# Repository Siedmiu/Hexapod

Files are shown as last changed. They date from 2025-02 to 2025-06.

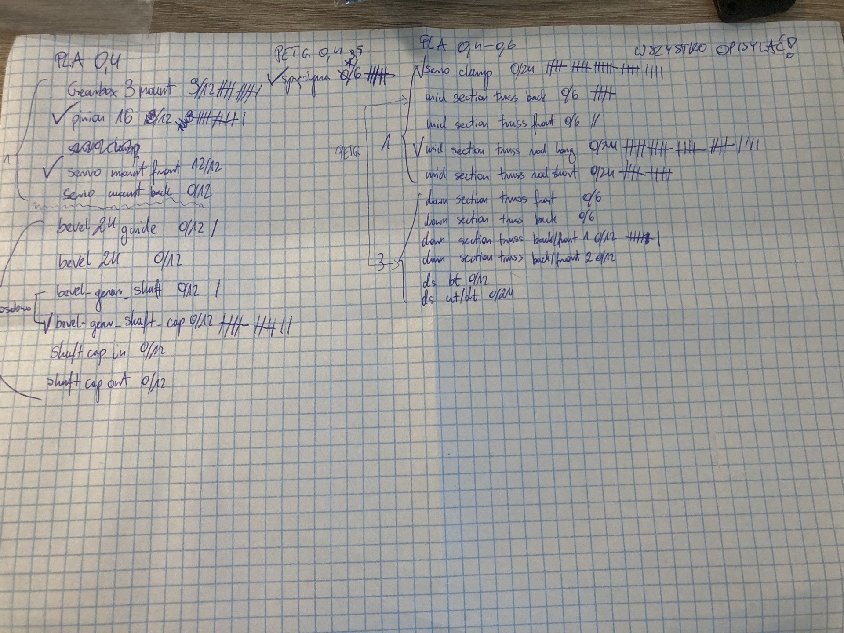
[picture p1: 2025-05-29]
hardware/3D models printing/DRUKOWANIE PROTO/printing progres/29.05.2025 _progress_note.jpg

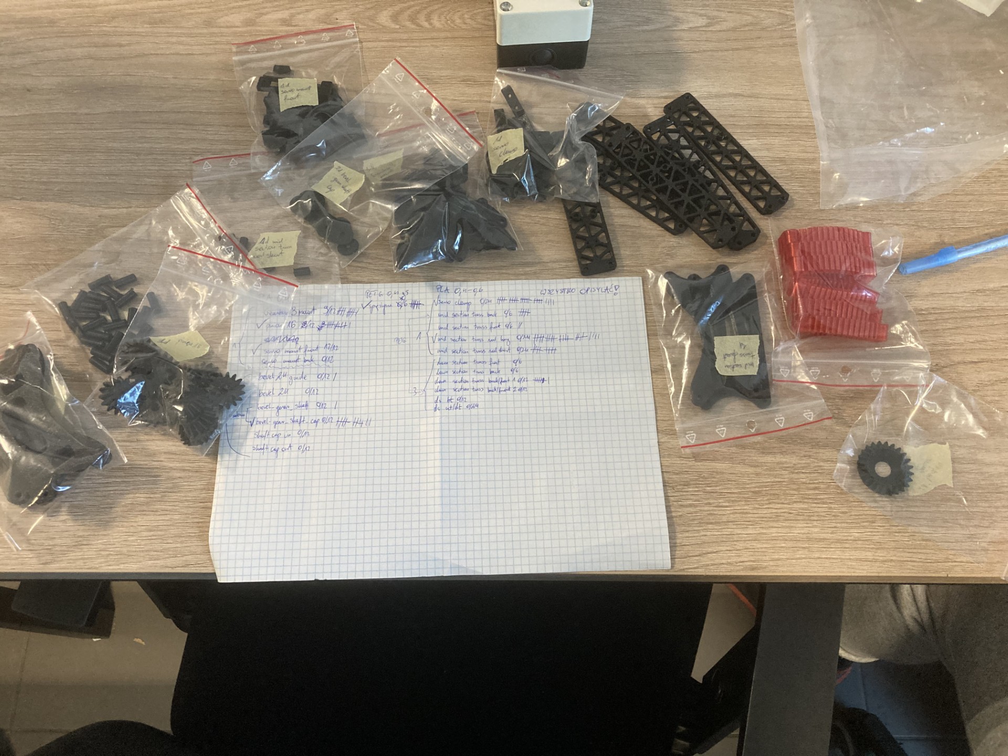
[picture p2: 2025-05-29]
hardware/3D models printing/DRUKOWANIE PROTO/printing progres/29.05.2025_printed_parts.jpg

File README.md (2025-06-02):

# Hexapod Robot Project

We are a group of students from Gdańsk University of Technology. Our goal is to create a 6 legged spider robot or a "Hexapod" in short.
Our current goals include the ability to **traverse difficult terrain**, **remote control** via an **android app**. Multiple walking algorithms are going to be implemented and tested.
Hexapod capabilities planned for the future include autonomous walking with the ability to follow objects and people using neural networks and computer vision algorithms.

Our simulation stack uses **ROS** and **Gazebo**, with **Python** for gait planning. The physical Hexapod is controlled by an **ESP32**, and all structural components are designed for **3D printing**.
For more information please visit our simulation repository: https://github.com/Siedmiu/Hexapod-Gazebo-Simulation

af067df6-a745-4674-9efd-3d1703f9f18c

## Milestone roadmap:

### Milestone I:
- [x] Complete Mechanical construction.
- [x] Preliminary simulation, ROS + Gazebo configured, single leg movement.

### Milestone II:
- [x] Production of parts and electronics procurement.
- [x] Hexapod assembly.
- [x] Simulating planned walking gaits.
- [x] Straight line walking tests.
- [x] ROS and manual remote control.

### Intermission -> New Design
- [x] New Hexapod Design.
- [x] Production of parts and electronics procurement.
- [x] Straight line walking simulation tests.
- [ ] Hexapod assembly.

### Milestone III:
- [ ] Full walk gait implementation.
- [ ] Tests and performance measurement.
- [ ] Finished project documentation.

Screenshots_2025-05-16-08-47-24

## Requirements:
Ubuntu 24.04 LTS, ROS Jazzy Jalisco, applicable Gazebo version

## Documentation and Setup:
Complete documentation, setup instructions, and Docker files will be available upon full release.

## Contributing:
This is a university-led project, and external contributions are not accepted until its conclusion.

## Related Repositories:
Android application repository: https://github.com/Siedmiu/Hexapod-Android-Application

Gazebo, Ros and simulation repository: https://github.com/Siedmiu/Hexapod-ROS2-System

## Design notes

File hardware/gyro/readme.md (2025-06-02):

These files contains code for acquiring and dealing with data provided by MPU-6050

gyro_write.ino is a script for Arduino to acquire data from gyroscope
Write.py is a script that writes the data to .csv file
traj.py calculates trajectory based of the data about angles and acceleration

============================================================================

_dmp files works as these above but are using DMP which provides better data

trajectory_integrated calculates trajectory using two data sets from IMU as now uses simple complementary filter

MPU-6050 datasheet: https://invensense.tdk.com/wp-content/uploads/2015/02/MPU-6000-Datasheet1.pdf

================19.04.2025==============
I am testing an alternative approach, and created new implementation.
The program runs through Matlab and directly connects to the esp, remember to define the COM port.

I want to use the onboard Digital Motion Processor (DMP) to get accurate orientation data while minimizing drift.

Data looks promising with minimal diviation and fast responses, but the acceleration scaling
needs to be fixed.

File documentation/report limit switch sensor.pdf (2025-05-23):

Autor: Mikołaj Goździelewski
Temat: Analiza możliwości implementacji krańcówki z elementem sprężystym w Gazebo

Celem jest zasymulowanie przełącznika krańcowego w środowisku Gazebo Harmonic, gdzie aktywacja krańcówki nie zachodzi bezpośrednio po dotknięciu ziemi, lecz po ugięciu elementu sprężystego. Oznacza to, że symulacja musi wykryć nie sam kontakt, lecz odpowiednio dużą siłę lub ugięcie wywołane naciskiem robota na podłoże.

## Potencjalne rozwiązania:

- model sprężyny + Contact Sensor
- Force-Torque Sensor

## Model sprężyny + Contact Sensor

Podejście polega na stworzeniu modelu sprężyny z wykorzystaniem „prismatic joint” i umieszczenie na jej końcu Contat Sensor. Pozwalałoby to na większy realizm symulacji oraz łatwą interpretację otrzymanych danych. Wadą rozwiązania jest duża złożoność modelu i możliwa niepotrzebna komplikacja symulacji. Rozwiązanie będzie bardzo wrażliwe na potencjalne rozbieżności modelu rzeczywistego i symulacyjnego jak i rozbieżności między fizyką w świecie realnym, a tą w programie.

## Force-Torque Sensor

Umieszczenie czujnika siły między dolną częścią nogi robota, a „podeszwą”, która w rzeczywistości nie istnieje. Rozwiązanie pozwala na dokładny pomiar siły i jest łatwe w integracji oraz nie wymaga dodatkowych skomplikowanych elementów jak działający model sprężyny. Wadą rozwiązania jest brak wizualizacji kontaktu, potencjalny problem z chwilową zmianą długości nogi oraz ręczne dobranie progu.

Wybrane rozwiązanie: Force-Torque Sensor
Uzasadnienie: Czujnik siły jest łatwiejszy w implementacji i mniej wrażliwy na potencjalne problemy z rozbieżnościami związanymi z fizyką w świecie rzeczywistym, a symulacji.

Wymagana konfiguracja:
Opcja 1 (inne dane z ROS dla programu z symulacji i robota):
- zdefiniowanie czujników siły w modelu dla każdej nogi
- skonfigurowanie mostu między Gazebo i ROS

- dodanie do kodu w python subskrypcji ROS, pobieranie wartości i przeliczanie ich Opcja 2:
- zdefiniowanie czujników siły w modelu dla każdej nogi
- napisanie własnego pluginu do Gazebo, który odczytywałby dane z API Gazebo i decydował czy jest siła wystarczająca do dotknięcia, a wtedy publikował wynik przez ROS

Plik XACRO:
Należy dodać wstawki <gazebo> w pliku, które będą wykorzystywane przez Gazebo podczas konwersji pliku URDF na SDF, wykorzystywany przez program.

Linki:
https://github.com/gazebosim/gz-sensors - repozytorium Gazebo o czujnikach, raczej nie przydatne
https://gazebosim.org/libs/sensors/ - strona Gazebo o czujnikach, pomocne jeśli nie wykorzystamy ROS do odczytów http://sdformat.org/spec?ver=1.12&elem=sensor#sensor_force_torque – strona SDF o czujnikach, przydatne do zmiany pliku XACRO https://gazebosim.org/api/sim/9/createsystemplugins.html - tutorial Gazebo o tworzeniu pluginów

Może przydatne linki do forów: https://robotics.stackexchange.com/questions/111546/need-for-gazebo-plugins-and-sdftutorial (https://robotics.stackexchange.com/questions/111546/need-for-gazebo-plugins-and-sdf-tutorial)
https://get-help.theconstruct.ai/t/documentation-for-gazebo-plugins/32571

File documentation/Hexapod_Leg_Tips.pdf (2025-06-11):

## High Friction Leg Tip Design for Walking Hexapod Robot: Design Process and Performance Evaluation

Grzegorz Lange

June 11, 2025

Abstract

This document presents the design process and performance evaluation of leg tip attachments for a walking hexapod robot. The primary objective was to address traction issues encountered on smooth and slippery surfaces through the development and testing of various rubber tip designs. Five different tip geometries were designed, manufactured, and tested: spherical base, flat base spherical, lattice spherical, flat with flower petals, and a hybrid design combining petals and lattice structures. Testing revealed that material selection is as critical as geometric design, leading to the development of silicone-based tips with TPU cores for optimal performance across various terrains.

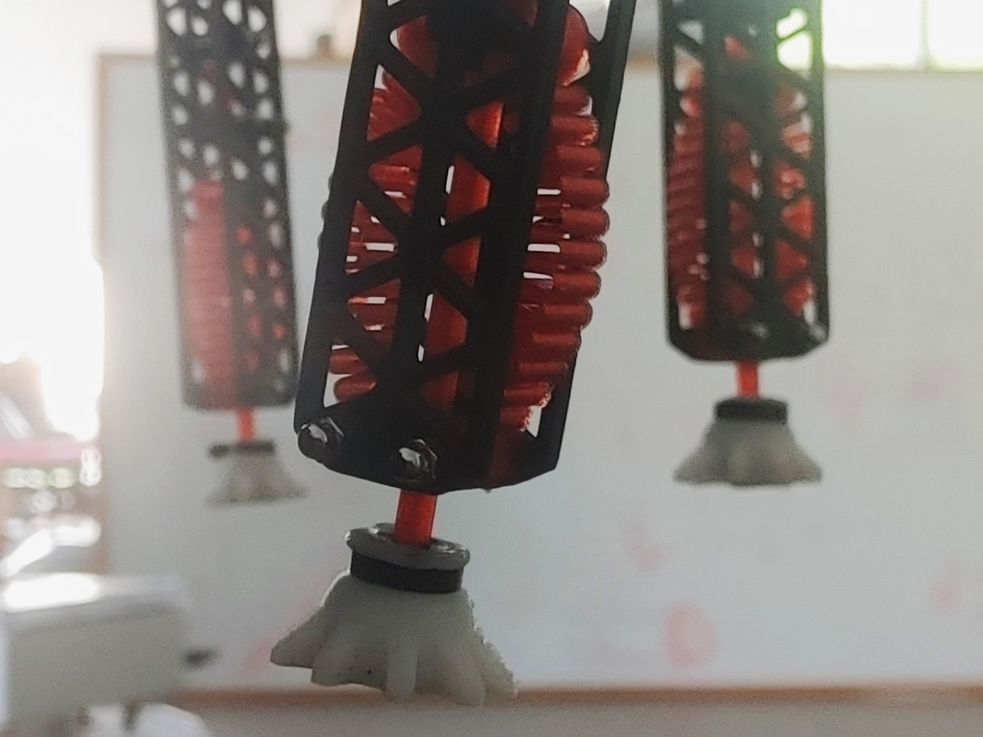
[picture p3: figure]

## 1 Introduction

Walking robots operating in diverse environments face significant challenges when encountering surfaces with varying friction characteristics. Hexapod robots, in particular, rely heavily on effective ground contact through their six legs to maintain stability and locomotion. This research addresses the critical issue of traction loss on smooth and slippery surfaces through systematic design and evaluation of specialized leg tip attachments.

### 1.1 Problem Statement

The hexapod robot experiences significant traction difficulties when operating on smooth surfaces such as polished floors, laminated surfaces, and other low-friction materials. These problems are amplified when dealing with small servomotors which are unable to maintain target position under heavy load. These conditions can lead to the following:

- Loss of locomotion control
- Reduced walking stability
- Inability to navigate certain terrains effectively
- Compromised performance of contact detection systems

### 1.2 Objectives

The primary objectives of this research are:

1. Design multiple leg tip geometries to improve surface traction
2. Evaluate performance across different surface types and conditions
3. Develop an optimal solution for indoor and outdoor applications

## 2 Design Methodology

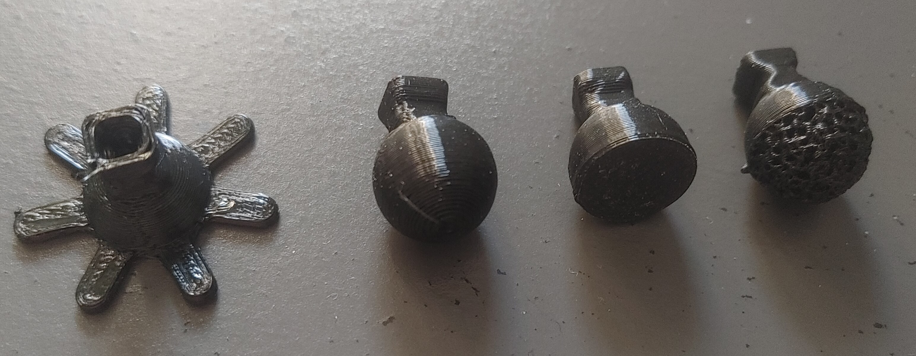
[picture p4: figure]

### 2.1 Design Concepts

Five distinct leg tip designs were developed and evaluated:

1. Spherical Base: Traditional rounded tip design serving as baseline
2. Flat Base Spherical: Flattened contact surface with spherical edges
3. Lattice Spherical: Spherical design with external lattice structure for deformation
4. Flat Flower Petals: Flat base with petal-like protrusions for increased contact area and adapt to angular changes
5. Hybrid (Petals + Lattice): Combined design incorporating both petal and lattice features

### 2.2 Material Selection

Two primary materials were investigated:

- TPU (Thermoplastic Polyurethane): Initial material choice for 3D printing capability. It is a soft material with great elastic deformation and a high coefficient of friction (COF).
- Silicone: Alternative material offering superior grip characteristics and high tackiness as a result of its high surface energy.

### 2.3 Manufacturing Process

### 2.3.1 TPU Components

TPU tips were manufactured using 3D printing technology, allowing complex internal geometries such as lattice structures and cavities. Custom Gcode approaches and advanced slicer features allowed for manufacturing exposed/external lattice structures creating textured surface for improved grip.

### 2.3.2 Silicone Components

Silicone tips were produced using custom molds for the external silicone lining combined with TPU cores for structural integrity. The manufacturing process involved

1. Mold design and fabrication
2. TPU core insertion for attachment interface
3. Silicone casting and curing

## 3 Testing and Evaluation

### 3.1 Testing Methodology

Performance evaluation was performed through single-leg testing on multiple types of surface. Each design was assessed using the following criteria:

- Deformation: Ability to conform to surface irregularities
- Contact Area: Maintenance of contact area under angular displacement
- Vertical Contact Area: Surface area in direct vertical contact
- Obstacle Hooking: Risks of engaging with surface features
- Terrain Penetration: Capability to penetrate soft surfaces and potential risks of jamming the legs into the ground.
- Shock Absorption: Energy dissipation during impact
- Dust/Sand Trap: Tendency to accumulate debris

### 3.2 Surface Types

Testing was carried out on the following surfaces:

- Smooth laminate
- Paper
- Hard foam
- Porous laminate

Due to the lack of professional testing equipment, friction performance was rated on a scale: low < medium < decent < good < excellent.

### 3.3 Shape Testing Results

Table 1: Design Characteristics and Mechanical Properties

Design | DeformationContact
Area/Angle

Vertical
Contact
Area

Obstacle
Hooking

Terrain Penetration

Shock Absorption

Dust/Sand
Trap
Spherical Base | Decent | Maintains same | Small | Low | Medium | Medium | No
Flat Base Spherical | Low | Low past certain an- gle | Large | Low | Low | Low | No
Lattice Spherical | Big | Maintains similar | Medium | Low | Medium | High | Yes
Flat + Flower Petals | Medium | Slightly decrease | Large | Medium/Low Low | Low | No
Hybrid | Big | Excellent | (remains
| | flat when tilted)
Large | Low | Low | Medium/Low Yes

Table 2: Surface Performance Comparison Across Different Materials

Design | Laminate Smooth | Paper | Hard Foam | Laminate Porous
Spherical Base | Low | Medium | Medium | Decent
Flat Base Spherical | Decent | Decent | Medium | Decent
Lattice Spherical | Low/Medium | Medium | Decent | Decent
Flat + Flower Petals | Decent | Decent | Medium | Decent
Hybrid | Decent | Decent | Medium | Medium

### 3.4 Shape Testing Key Findings

### 3.4.1 Flat Base

Flat base approach greatly increases the contact surface area, however it struggles with maintaining it even at shallow angles.

### 3.4.2 Flat Base with Flower Petals

Flower petals were added to directly address the issue with maintaining the contact surface area. The idea behind the flower petals is that, once the angle increases the flower petal will drag and deform the main tip surface.

### 3.4.3 Lattice structures

Incorporating the external lattice structure resulted in improvements in both traction and deformation. The open latices however have a tendency to accumulate sand and derbies, which results in sharp decline in performance. This approach is only suitable for clean environments and possible only using 3D printing technology.

### 3.4.4 Hybrid Design

The hybrid design combining petals and lattice structure demonstrated superior performance in maintaining contact area under angular displacement while providing adequate deformation characteristics.

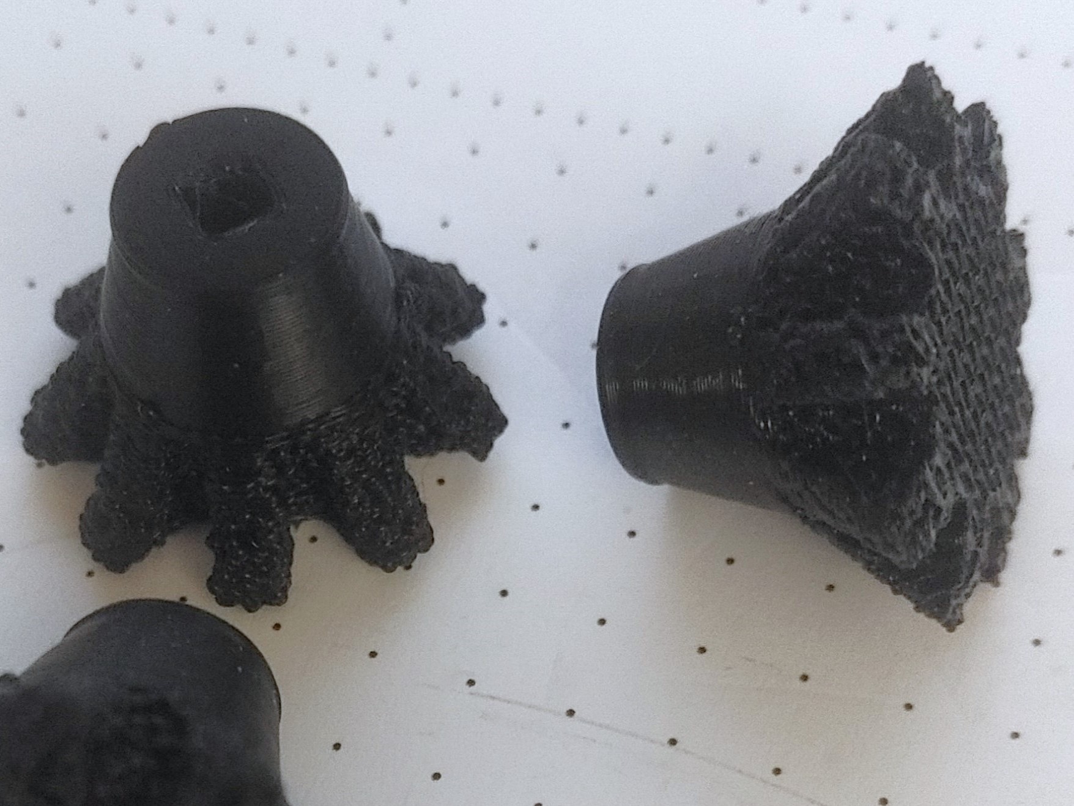
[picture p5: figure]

### 3.4.5 TPU Material Limitations

Despite geometric optimizations, TPU material exhibited insufficient grip on smooth surfaces, particularly on laminated floors where the robot continued to experience significant slipping.

### 3.4.6 Vertical Shock Absorption

The tip designs were engineered to exhibit poor vertical shock absorption performance. This approach was chosen to ensure predictability, since our Hexapod relies on shock absorbing springs coupled with contact detection switches. Allowing to much vertical compression of the tip could result in it getting twisted or sprained and loosing balance.

## 4 Material Transition and Optimization

### 4.1 Silicone Implementation

Based on testing results indicating material limitations, the design process transitioned to silicone-based tips. Key advantages of silicone include:

- Superior surface grip compared to TPU
- Enhanced deformation characteristics
- Better conformability to surface irregularities
- Reduced slipping on smooth surfaces

### 4.2 Hybrid Material Approach

The final design incorporates a hybrid material strategy:

- Silicone exterior: Provides optimal grip and deformation
- TPU core: Ensures structural stability and provides reliable attachment interface
- Elimination of vertical compression: TPU core prevents excessive deformation under load

### 4.3 Design Evolution

The silicone implementation underwent iterative improvement:

1. Initial silicone molding based on hybrid TPU design
2. Volume optimization: Second generation increased to 215% of original volume, for reliability the contact area should be as big as possible
3. Edge rounding to prevent stress concentration and cracking of the cast
4. Improved mold design for consistent manufacturing

### 4.4 Final Design

The final design consists of flat bottom surface with radially distributed petals structures that are connected via solid lofts to the main shaft. The tip has internal TPU core that extends up to 80 percent of the body. The design maximizes the contact area and conforms to the surface.

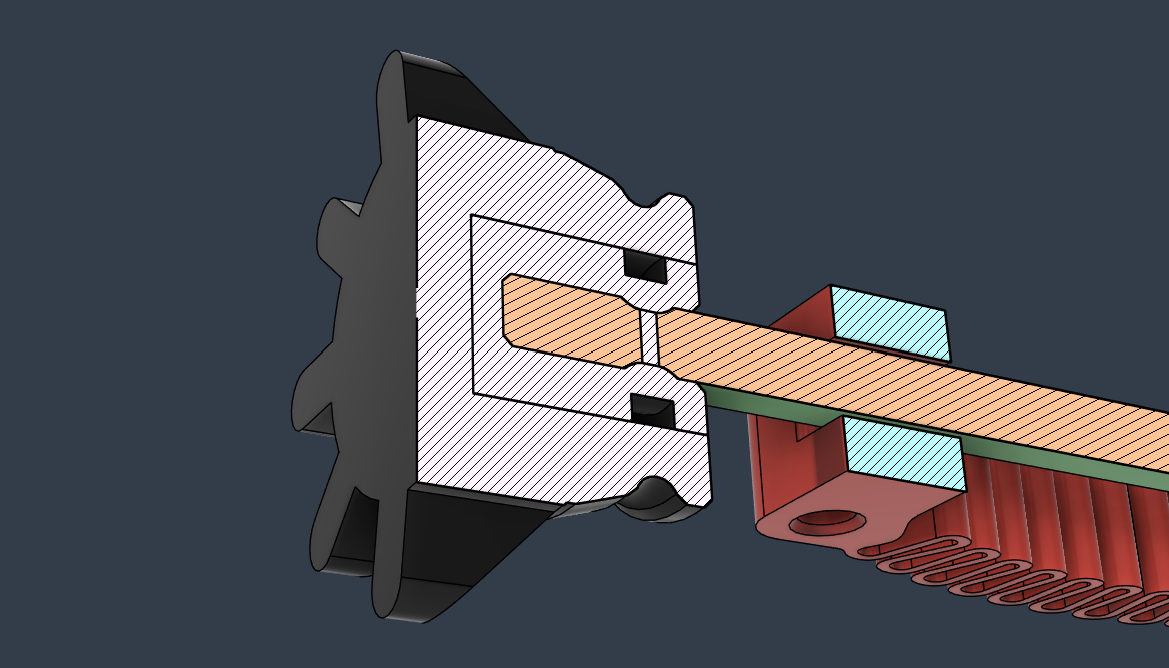
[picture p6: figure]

### 4.5 Final Design Tests

The design showed excellent friction performance on all of the tested surfaces. The TPU core decreased the vertical deformation, and it was rated as ”Medium” compared to other designs. The contact area was large and the main body of the tip is capable of maintaining its vertical position with relation to the ground for shallow angles. For larger angles the contact area decreases only slightly. The risks of terrain penetration and obstacle hooking are minimal, Dust and sand might stick to the surface, but is easy to clean.

## 5 Results and Discussion

### 5.1 Performance Validation

Testing confirmed the theoretical predictions regarding material performance:

- TPU designs, despite geometric optimization, remained insufficient for smooth surface traction
- Silicone implementation dramatically improved grip performance
- Hybrid material approach successfully balanced grip and structural integrity

### 5.2 Design Trade-offs

The evaluation revealed several important trade-offs:

- Deformation vs. Stability: Higher deformation improves surface conformity but may compromise structural stability
- Contact Area vs. Angular Performance: Larger flat surfaces provide better vertical contact but may lose effectiveness at angles
- Grip vs. Debris Accumulation: Designs with textures provide better grip characteristics but tend to trap more dust and sand

## 6 Conclusions and Possible Improvements

### 6.1 Conclusions

1. The hybrid design combining petals and lattice structure provides optimal geometric characteristics for indoor applications
2. Material selection is equally critical as geometric design for overall performance
3. Silicone material significantly outperforms TPU in terms of surface grip
4. Hybrid material approach (silicone exterior with TPU core) offers the best balance of performance characteristics
5. Develop surface-specific tip variants for specialized applications

### 6.2 Future Work

Future research directions include:

- Designs with surface dimples and or protrusions
- Designs with variable suction cups
- Investigation of smart materials for adaptive grip characteristics
- Integration of sensory capabilities within tip structures
- Long-term durability testing under operational conditions

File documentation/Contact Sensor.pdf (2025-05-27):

## Contact Sensor w Gazebo

Wstęp:
Celem zadania jest dodanie do symulacji czujników stykowych na nogach robota, które będą publikowały na wybranych topicach Gazebo informacje o kolizji. Doszło do niewielkiej zmiany planów względem raportu na temat researchu jak zrealizować w symulacji czujniki krańcowe ze sprężynkami. W tamtym tekście zdecydowałem o wykorzystaniu czujników siły, ale po naradzie z członkami grupy doszliśmy do wniosku, że uproszczenie zadania do czujniku stykowego nie powinno stanowić większego problemu. Na starcie muszę zaznaczyć, że zadanie nie zostało jeszcze wykonane. Do dokładniejszego zrozumienia tematu na szybko opiszę rzeczy, które uznałem za istotne do zrozumienia dalszego tekstu. Symulacja Gazebo składa się z plików Xacro, które opisują robota, pliku SDF, który opisuje świat oraz plików pythonowych, które pozwalają na uruchomienie symulacji. Pliki Xacro mają na celu usprawnienie pisania opisów robotów, dzięki zastosowaniu tagów MACRO, które są swego rodzaju funkcjami, które można wywołać przesyłając swoje parametry. Jedynym systemem plików obsługiwanym przez Gazebo jest SDF, co prowadzi do dużego problemu i konieczności translacji pliku Xacro na SDF, co niestety nie jest możliwe, gdyż Xacro opisuje nie plik SDF, a URDF, wymagany do innych programów. Translacja odbywa się przez najpierw zamianę Xacro na URDF, a następnie URDF na SDF. Translacje te można wykonać również komendami:

Translacja Xacro na URDF:
ros2 run xacro xacro nazwa_pliku.xacro > nazwa_pliku.urdf
Translacja URDF na SDF:
gz sdf -p nazwa_pliku.urdf > nazwa_pliku.sdf

Problemy (informacje zawarte w tym segmencie niekoniecznie są poprawne, są one tylko i wyłącznie moimi przemyśleniami, zdobytymi na bazie kilku godzin prób dodania czujników, szukania informacji na ich temat w internecie oraz konsultacji z ChatemGPT):

- Pluginy – do poprawnego korzystania z czujników styku potrzebne są odpowiednie pluginy, które należy dodać do pliku SDF, który opisuje świat, plugin czujnika styku to:
<plugin
filename="gz-sim-contact-system"
name="gz::sim::systems::Contact">
</plugin>
Niestety dodanie tego pluginu prawdopodobnie spowoduje błędy, skutkujące niepoprawnym uruchamianiem symulacji, jest to spowodowane tym, że domyślnie Gazebo korzysta z różnych pluginów, ale dodając własny domyślne nie są już wczytywane i należy dodać je własnoręcznie są to pluginy:
<plugin
filename="gz-sim-physics-system"
name="gz::sim::systems::Physics"> </plugin>
<plugin
filename="gz-sim-scene-broadcaster-system" name="gz::sim::systems::SceneBroadcaster"> </plugin>
<plugin
filename="gz-sim-user-commands-system" name="gz::sim::systems::UserCommands"> </plugin>

- Plik opisujący świat – możliwym problemem może również być brak lub niepoprawne zdefiniowanie pola kolizyjnego podłogi, powód zostanie dokładniej opisany w podpunkcie „Topic czujnika”
- Znacznik Gazebo – przez pisanie opisu robota w Xacro, a nie w SDF jest potrzeba korzystania ze znaczników <gazebo>, niestety tutaj pojawia się problem. Użycie znacznika <sensor> wewnątrz samego znacznika <gazebo> nie pozwoli na dodanie czujnika, podczas translacji z pliku URDF na SDF interpreter ignoruje wszystko czego nie rozumie, a nie rozumie znacznika <sensor>, więc ta sekcja zniknie w wynikowym pliku SDF, żeby tego uniknąć należy skorzystać ze znacznika <gazebo reference=”nazwa_linku”>. Taka składnia zmusza interpreter do umieszczenia zawartego segmentu wewnątrz linku, co spowoduje pojawienie się jego w drzewku opisującym model z GUI(interfejs graficzny) Gazebo.
Przykład składni:
<gazebo reference="nazwa_linku">
<sensor name='nazwa_sensoru' type='contact'> <contact>
<collision>nazwa_pola_kolizyjnego</collision> <topic>/nazwa_topic</topic>
</contact>
<always_on>1</always_on>
<update_rate>100</update_rate>
</sensor>
</gazebo>
- Problemy ze znacznikiem <collision> - do poprawnego działania czujnika styku, należy mu przypisać odpowiednie pole kolizyjne zawarte w znaczniku <collision>. W przypadku korzystania z plików Xacro oraz jointów typu „fixed”, podczas translacji dochodzi do zmian nazw pól kolizyjnych, co prowadzi do niepoprawnego określania pola przypisanego do czujnika. Nową nazwę pola kolizyjnego można sprawdzić w drzewku opisującym model w GUI Gazebo. Możliwy jest również problem z samą definicją pola kolizyjnego, gdyż na wszystkich znalezionych przeze mnie przykładach czujnik stosowany jest na prostych obiektach z prostymi polami kolizyjnymi złożonymi z pojedynczych znaczników <collision>, w naszym przypadku korzystamy z pola kolizyjnego składającego się z kilku znaczników <collision> co może być problemem.
- Topic czujnika – topic czujnika styku w Gazebo publikuje tylko w momencie wykrycia kolizji między przypisanym pole, kolizyjnym, a innym obiektem. Istnieje więc możliwość, że topic czujnika nie pojawia się z powodu złej definicji pola kolizyjnego lub braku odpowiedniej kolizji.
- Dokumentacja i przykłady – realizacji zadania nie ułatwia brak jakiejkolwiek sensownej dokumentacji lub przykładów. Gazebo Harmonic jest dość nowa, co powoduje problemy ze znalezieniem jakichkolwiek informacji o działaniu programu, a już szczególnie przykładów choć trochę zbliżonych skomplikowaniem do projektu „Hexapod”, powoduje to w dużej mierze działanie sposobem prób i błędów, poruszając się na oślep nie mając pojęcia, czy dana zmiana faktycznie przybliża do ukończenia zadania, czy może psuje kolejny element układanki.

Podsumowanie:
Nie udało mi się osiągnąć działającego czujnika styku w Gazebo i nie mam pojęcia gdzie może tkwić problem. Jest kilka potencjalnych miejsc, gdzie dochodzi do błędu, a są to:
- złe umieszczenie lub zdefiniowanie pluginu dla czujnika
- złe przypisanie pola kolizyjnego do czujnika
- źle zdefiniowanie pola kolizyjnego, niewystarczająca ilość danych dla Gazebo
- brak kolizji między polem kolizyjnym, a podłogą, co powoduje brak nadawania topicu czujnika
- brak lub zła definicja pola kolizyjnego podłogi w pliku opisującym świat.

A kto zrobi poprawnie działający Contact Sensor w Gazebo?
No WY
Pozdrawiam dr inż. Krzysztofa Nowickiego

Przydatne(lub nie) linki:
Działający Contact Sensor dla prostego modelu (plik SDF) https://github.com/gazebosim/gz-sim/blob/gz-sim8/examples/worlds/contact_sensor.sdf Dokumentacja Gazebo Harmonic na temat czujników: https://gazebosim.org/docs/harmonic/sensors/

Autor: Mikołaj Goździelewski

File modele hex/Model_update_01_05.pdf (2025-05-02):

Model update 01.05.2025

In order improve consistency, reduce reliance on precise tolerances, and reinforce the first joint, several changes have been made to the model.
The impact that those changes have on the simulation is negligible.

Joint 0 changes:

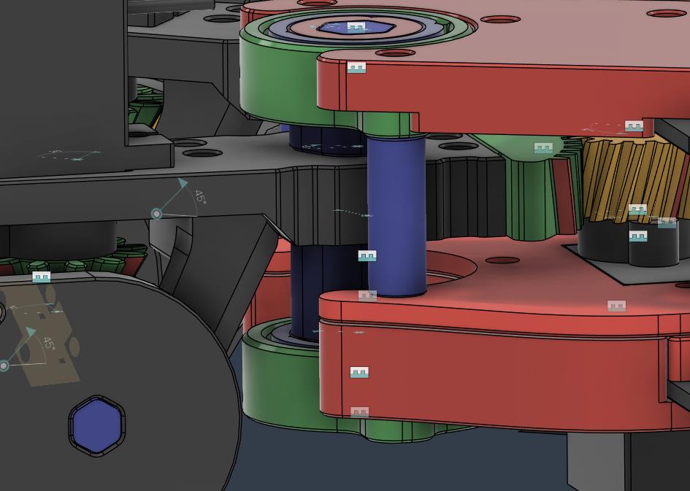
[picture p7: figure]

The mounting bolt hole on the “up section/leg attachment/servo holder” has been relocated to ensure space for a new set of reinforcement roods. The rods prevent tension build-up from the torque (Y CCW for left legs of the hexapod) when the legs are lifted off the ground.
Together with slots on the servo holder, the rods limit the motion preventing de-meshing of the gears.

Joint 3 changes:

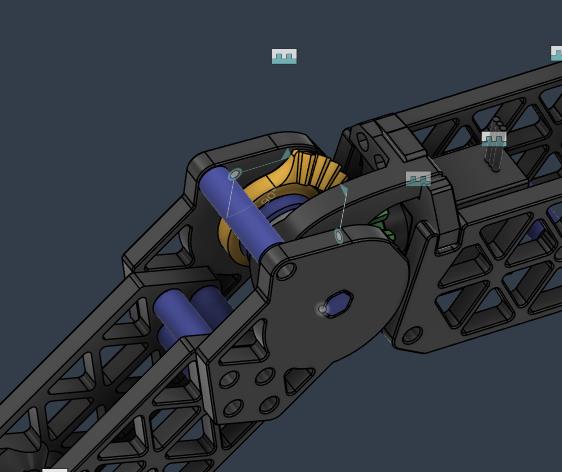
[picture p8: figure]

New reinforcement rod has been added to ensure that the material won’t bend outwards and skip a step on the gear assembly. This rod also prevents de-meshing of the gear assembly when a CCW rotation is applied past the range of motion.

Bug fixes:
Fixed missing holes on the platform mounting clips and bearing center hexagonal holes that were created due to an incorrect way that the Fusion handles downstream changes.

Misc:
Reduced the radius of the ball bearings mounting parts.
Changed how rods tolerance is calculated.
Numerous small changes with no downstream effect.

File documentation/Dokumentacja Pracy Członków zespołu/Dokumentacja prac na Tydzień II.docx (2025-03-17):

# Dokumentacja prac na Tydzień II

Skrócony spis prac wykonanych przez członków zespołu:

- Mariia Krykun: prace nad symulacją w ROS2; Komunikacja ROS2 z ESP32, przesyłanie obliczeń
- Bartłomiej Bąk: Symulacja python ruchu i kolizji
- Bartosz Babiński: Nauka i prace nad symulacją w Gazebo; Integracja modelu w Gazebo
- Grzegorz Lange: Poprawki mechaniczne; Projekt łożysk
- Julia Hrycyna: Symulacja Python ruchu w 2D i 3D
- Mateusz Boniecki: Nauka Kotlin + prace nad aplikacją
- Mikołaj Goździelewski: Integracja modelu w Gazebo; Nauka i research Gazebo
- Natan Tułodziecki: Kurs Android Studio; wybór MK
- Miłosz Kaszubowski: Wyliczenia prądowe; Wybór dostawców elementów
- Paulina Lokś: Kurs Android Studio

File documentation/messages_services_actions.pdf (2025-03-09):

Communication in ROS

Effective communication between different modules is crucial in a robotic system, enabling seamless data exchange and coordination. In ROS (Robot Operating System), three primary communication methods facilitate interactions between different components: messages, services, and actions. Each method serves a unique purpose, depending on whether the communication needs to be continuous, request-based, or interactive with feedback.

Example of a Trash-Picking Robot

To understand how these communication methods work, consider a trash-picking robot. This robot continuously detects trash, moves toward it, picks it up, and deposits it into a bin. Its software consists of three key modules:

1. Perception – Detects and identifies
trash.
2. Brain – Processes the perception data and decides on actions.
3. Actuation – Controls the robot’s
movement and physical interactions.

For the robot to function correctly, these

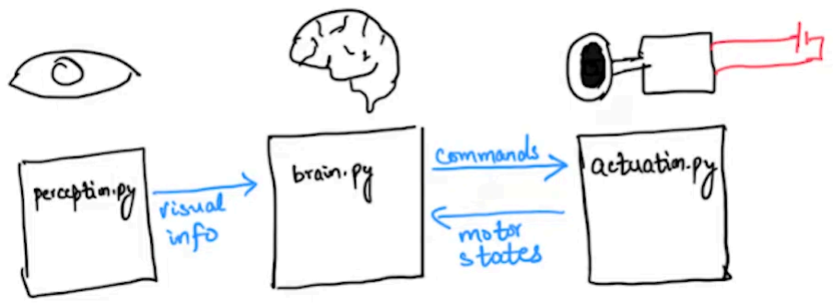
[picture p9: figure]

modules must exchange data efficiently. The perception module must communicate visual information to the brain, the brain must send movement commands to the actuation module, and the actuation module must report motor states, such as battery levels, back to the brain.

Communication Method 1: Messages (Topics)

One of the fundamental communication methods in ROS is message passing via topics. A topic acts as a channel where one module publishes data, and other modules subscribe to receive updates. This model is useful for continuous, asynchronous data exchange.

- In the trash-picking robot, the perception module publishes trash detection data on a specific topic.
- The brain subscribes to this topic, staying updated on detected trash.
- This setup ensures that whenever the perception module identifies trash, the brain module immediately receives the information.

The key characteristic of topic-based messaging is asynchronous communication—the publisher can send updates at any time, and subscribers receive them as they occur without needing to request data explicitly.

Communication Method 2: Services

Unlike topics, services allow a module to request specific information or trigger an action from another module in a client-server model. This method is useful for request-response interactions rather than continuous data flow.

- In the trash-picking robot, the brain may need to check the battery status before executing a movement command.
- The brain sends a request to the actuation module (server) to retrieve battery information.
- The actuation module responds with the requested battery level.

This approach ensures that the brain only retrieves the data when necessary, reducing unnecessary data transmission. Services also support requests with parameters, allowing for specific queries (e.g., checking the battery level of a particular motor).

Communication Method 3: Actions

Actions are a more advanced communication method used for tasks that require feedback and the ability to cancel execution. Unlike services, which are single request-response interactions, actions provide ongoing status updates during task execution.

- Suppose the brain instructs the actuation module to move the robot to a specific position.
- The actuation module continuously sends feedback about the robot’s current location.
- If needed, the brain can cancel the movement command mid-execution—a feature not available with services.

Actions are particularly useful for long-running operations where real-time monitoring is necessary, such as motion control, navigation, and robotic arm manipulation.

Differences in ROS Versions

One notable difference between ROS 1 and ROS 2 is how they handle service calls. In ROS 1, service calls are blocking, meaning the system must wait for a response before proceeding. In ROS 2, non-blocking calls allow the program to continue execution while waiting for a response, improving efficiency in distributed systems.

Conclusion

ROS provides three primary communication methods to handle different types of interactions in a robotic system:

1. Messages (Topics) – Used for continuous, asynchronous data sharing.
2. Services – Best suited for request-response interactions.
3. Actions – Ideal for tasks requiring feedback and the ability to cancel execution.

Choosing the appropriate method depends on the specific needs of the system. Understanding these communication mechanisms is essential for designing efficient, scalable robotic applications.

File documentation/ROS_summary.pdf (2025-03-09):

Understanding ROS: The Robot Operating System

What is ROS?

ROS (Robot Operating System) is a widely used middleware designed to simplify the development of robotic systems. While it is not a traditional operating system, it provides essential tools and services that help manage communication between different components in a robotic system. ROS facilitates message passing, package management, and hardware abstraction, making it easier for developers to build complex robotic applications.

The Need for ROS

Robotic systems often consist of multiple independent modules that must work together efficiently. Without a structured framework, managing communication and coordination between these components can be challenging. ROS was created to address this issue by offering a standardized way to handle inter-process communication, ensuring seamless data exchange between various parts of a robot.

Example of a Robotic System

A useful way to understand ROS is by considering a humanoid trash-picking robot. This robot needs to perform tasks such as scanning the environment for trash, moving toward it, picking it up, and placing it in a bin. Its software stack can be divided into three key modules:

1. Perception – Detects and identifies trash in the environment.
2. Brain – Acts as the decision-making center, processing information from perception and determining the next action.
3. Actuation – Controls movement and executes the actions planned by the brain.

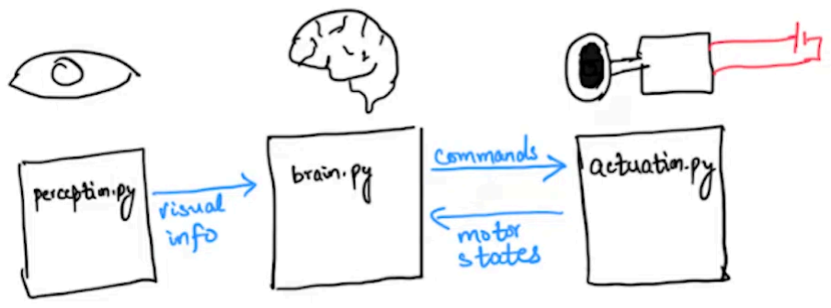
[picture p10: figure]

Efficient communication between these modules is critical for the robot to function correctly. The perception module informs the brain about detected trash, and the brain then instructs the actuation module to move accordingly.

Communication Methods in Robotic Systems

Two common methods are used to enable communication between different modules in a robotic system:

- Polling: The perception module continuously checks for trash and updates a shared memory location. The brain and actuation modules repeatedly check this memory to get updates. While functional, polling can be inefficient due to constant processing.
- Interrupts: A more efficient approach where modules only respond when an update occurs, reducing unnecessary processing and improving system responsiveness.

ROS helps manage these communication methods by providing a structured messaging system, ensuring efficient data exchange without requiring developers to handle low-level communication details manually.

ROS as Middleware

As middleware, ROS simplifies the process of integrating multiple components within a robotic system. It allows developers to focus on building individual modules without worrying about how they communicate. This abstraction is especially useful in distributed robotic systems, where different processes run independently but must share information in real time.

Package Management in ROS

ROS uses a package-based system to organize different functionalities into modular components. These packages contain specific functionalities such as motion control, sensor processing, or navigation.

- In ROS1, Catkin is the tool used for package management.
- In ROS2, Colcon is introduced, providing improved build efficiency and better dependency management.

This modular structure makes it easier for developers to maintain, reuse, and share components across different robotic projects.

Hardware Abstraction

ROS also provides a layer of hardware abstraction, allowing developers to integrate various hardware components without needing to understand their low-level details. Packages can be created to include drivers and embedded code for specific hardware, and these packages expose standardized ROS APIs. This makes it easier for other developers to use the hardware without directly interacting with its internal workings.

Open-Source Community and Reusable Packages

One of the biggest advantages of ROS is its large open-source community. Many pre-built ROS packages exist for common robotic functionalities, such as localization, mapping, and navigation. These packages can be used as plug-and-play modules, accelerating development and reducing the need to build everything from scratch. However, for specialized applications, custom ROS packages may still be necessary.

Conclusion

ROS plays a crucial role in modern robotics by providing a standardized framework for communication, package management, and hardware abstraction. It enables developers to build complex robotic systems more efficiently while benefiting from a vast open-source ecosystem. Understanding ROS is essential for anyone working with robotic applications, as it simplifies both software and hardware integration, making robotic development more accessible and scalable.

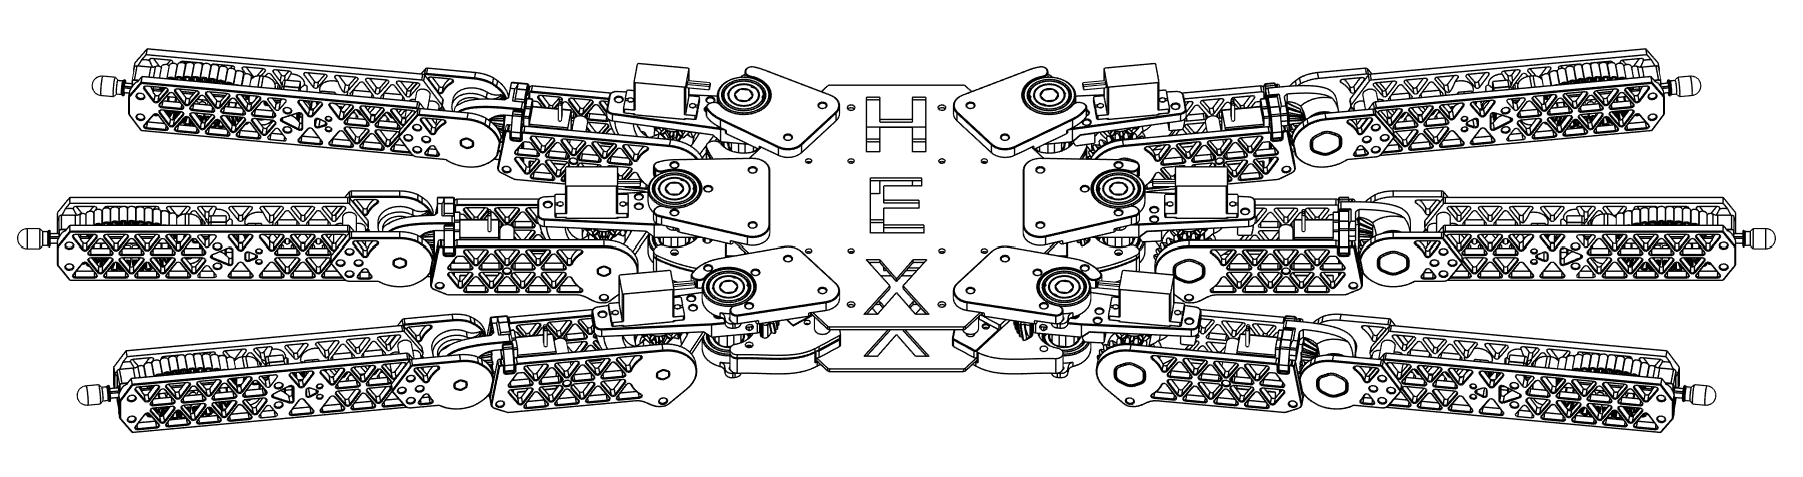
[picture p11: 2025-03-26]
images_new/straight.PNG

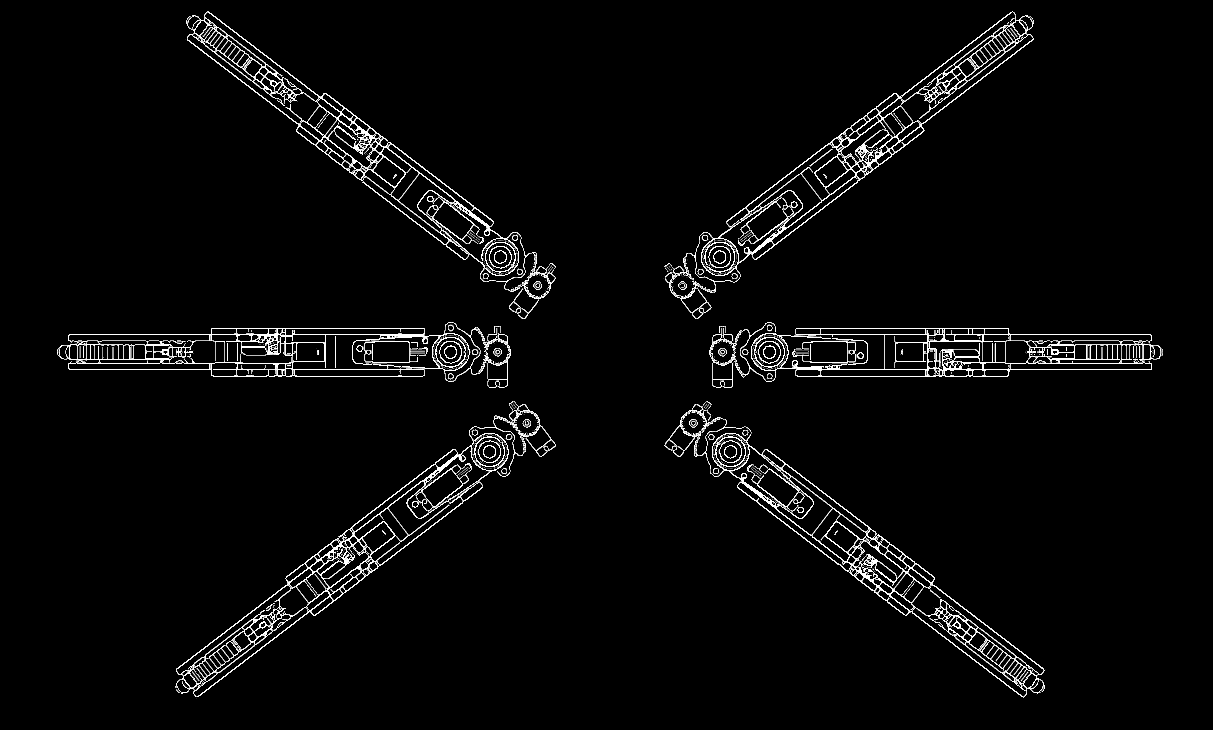
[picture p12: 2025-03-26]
images_new/top_legs_processed.png

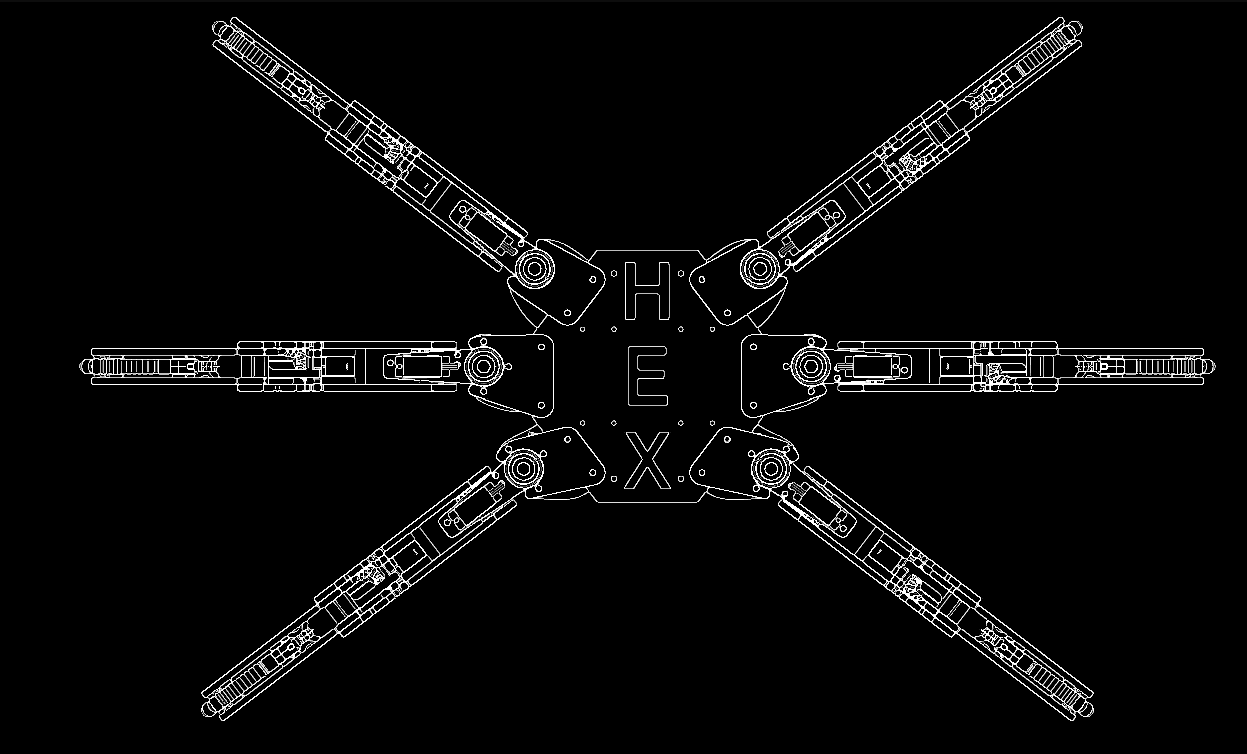
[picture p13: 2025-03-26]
images_new/full_top.PNG

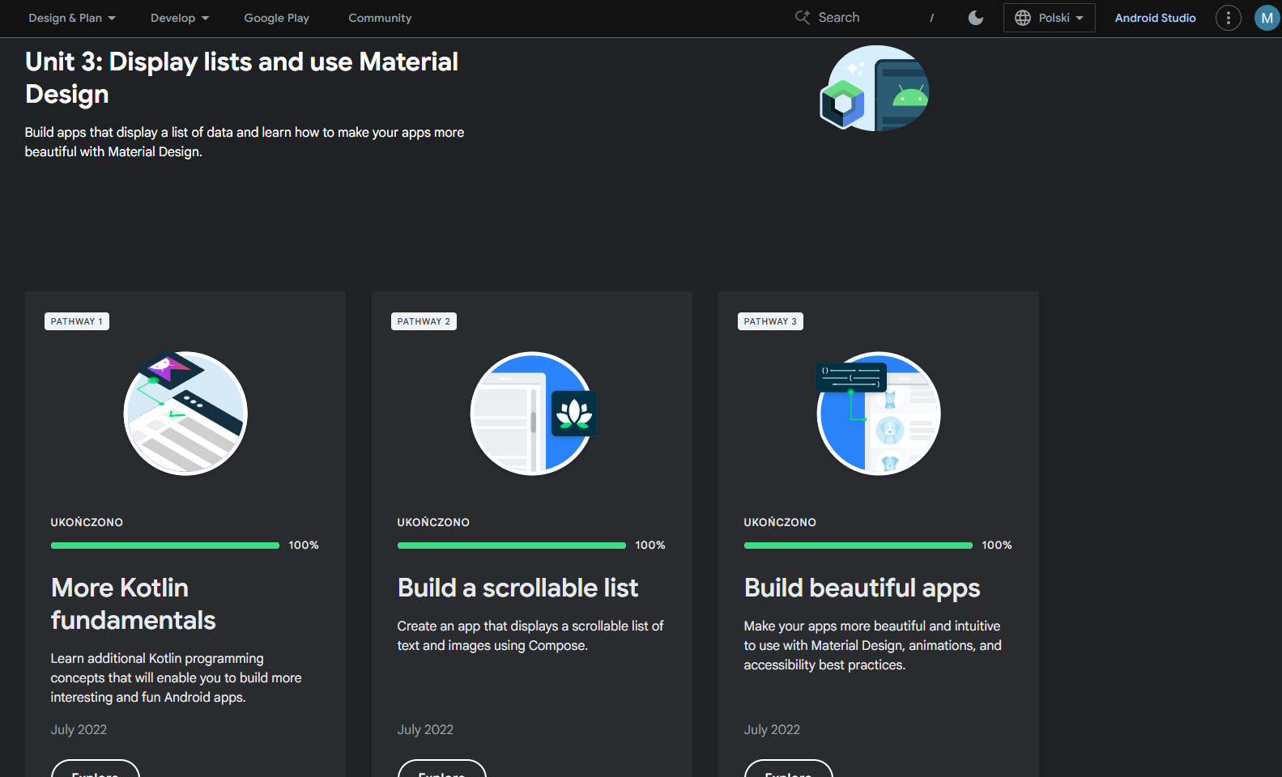
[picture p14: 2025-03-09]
documentation/Dokumentacja Pracy Członków zespołu/learning/Android Basics with Compose/Zrzut ekranu 2025-03-09 144319.png

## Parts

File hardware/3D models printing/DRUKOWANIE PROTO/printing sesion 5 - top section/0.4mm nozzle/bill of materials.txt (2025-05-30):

==========0.4==============
//bez kulek łożyskowych nie powinno być tarcia między elementami
// bearing outside(cage bottom(bearing inside))
bearing inside.stl		x12
bearing outside.stl		x12
cage bottom.stl			x12

Spur 16.stl			x6
Spur 32.stl			x6
Vertical Shaft.stl		x6

==========0.4 or 0.6========
Bearing Cap Up.stl		x6
Top Section Holder.stl		x6 //"kropelka" ustawiona ogonkiem do góry
Top Section Truss Back.stl	x6
Top Section Truss Front.stl	x6

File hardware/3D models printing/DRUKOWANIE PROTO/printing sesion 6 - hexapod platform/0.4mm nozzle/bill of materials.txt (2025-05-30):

==========0.4==============
support rod small.stl		x12
support rod.stl			x12
==========0.4 or 0.6========
Platform Top.stl		x1 (drukuje Miłosz)
Platform Down.stl		x1 (drukuje Miłosz)
bearing mount L0-5 down/top.stl x6 (każdy plik raz, drukuje Grzegorz)

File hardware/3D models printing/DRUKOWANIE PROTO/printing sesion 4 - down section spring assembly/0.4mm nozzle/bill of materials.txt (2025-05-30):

Części symeryczne oznaczone "/"

rod holder back/front.stl 	x12
Spring Rod.stl			x6
switch holder back/front.stl	x12
Spring				x6 already printed

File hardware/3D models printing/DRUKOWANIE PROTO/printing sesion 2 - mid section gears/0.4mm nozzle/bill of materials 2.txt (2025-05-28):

bevel 24 guide.stl 	x12
bevel 24.stl 		x12
Bevel_gear_shaft.stl 	x12
Bevel_gear_shaft_cap.stlx12
shaft cap in.stl 	x12
shaft cap out.stl 	x12

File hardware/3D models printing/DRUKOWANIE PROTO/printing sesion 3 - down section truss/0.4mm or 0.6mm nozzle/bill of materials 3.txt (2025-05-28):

Części symeryczne oznaczone "/"

Down Section Truss Front.stl 		x6
Down Section Truss Back.stl 		x6
Down Section Truss Back/Front 1.stl	x12
Down Section Truss Back/Front 2.stl	x12
ds bt.stl				x12
ds ut/dt.stl				x24

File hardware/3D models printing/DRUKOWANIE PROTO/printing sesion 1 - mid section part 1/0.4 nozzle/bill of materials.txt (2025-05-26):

KOPIA PLIKU DLA WYGODY

0.4 or 0.6 nozzle:
Mid Section Truss Back.stl x6
Mid Section Truss Front.stl x6
mid section truss rod long (identyczne modele) -> 24 sztuki
mid section truss rod short (identyczne modele) -> 24 sztuki
servo clamp.stl x24

0.4 nozzle:
servo mount back.stl x12
servo mount front.stl x12
pinion 16.stl x12
Gearbox 3 Mount.stl x12

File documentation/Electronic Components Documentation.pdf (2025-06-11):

# Electronic Components Documentation

### Project: [Your Project Name]

### June 11, 2025

## Contents

1 Overview | 2
2 Components | 2
3 Electrical Wiring Diagram | 3

## 1 Overview

This document describes the electronic components used in our project, along with their specifications and roles. The system is based on an ESP32 controller and includes servos, PWM drivers, sensors, and switches.

## 2 Components

### 2.1 MG996R Servo Motors (x18)

- Type: Digital high torque servo
- Operating Voltage: 4.8V–7.2V
- Stall Torque: Up to 11 kg.cm @ 6V
- Control Signal: PWM (Pulse Width Modulation)
- Application: Movement control (e.g., limbs, joints)

### 2.2 PCA9685 PWM Controller (x2)

- Channels: 16-channel 12-bit PWM
- Communication: I²C interface
- Power Supply: 5V logic level
- Used for controlling up to 32 servos with only two I²C addresses

### 2.3 POS-150-5-C Power Supply

- Output Voltage: 5V
- Output Current: Up to 30A (150W total)
- Usage: Powers servos and PCA9685 boards

### 2.4 Micro Endstop Switches (x6)

- Type: Momentary mechanical switches
- Usage: Limit/end position detection
- Triggered when component reaches physical boundary

### 2.5 ESP32-WROVER-DEV

- Microcontroller with Wi-Fi and Bluetooth
- Extra RAM (4MB PSRAM)
- GPIO, I²C, SPI support
- Central controller for the system

### 2.6 MPU6050 Accelerometers (x2)

- 3-axis gyroscope and 3-axis accelerometer
- Communication: I²C
- Used for motion sensing and orientation

## 3 Electrical Wiring Diagram

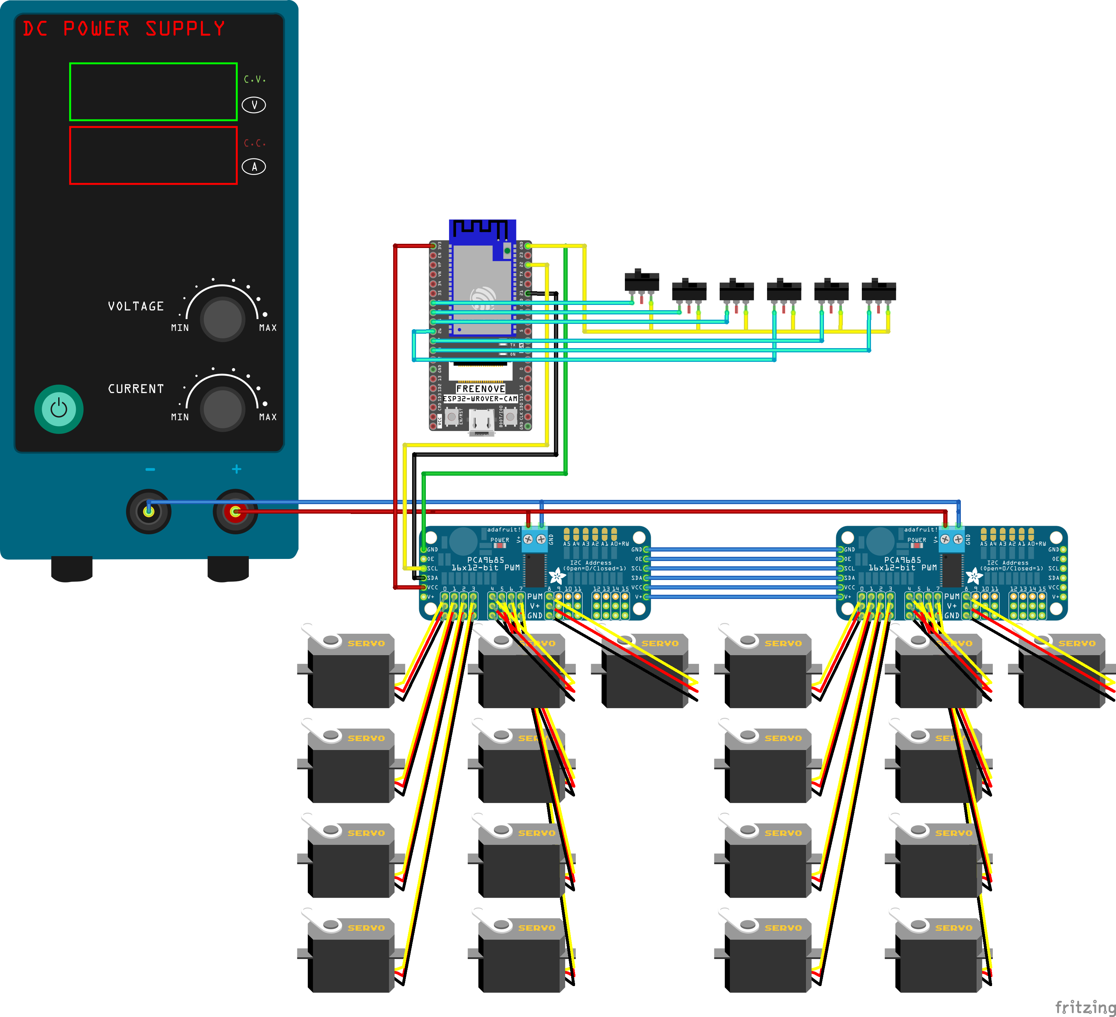
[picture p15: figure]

Figure 1: Wiring Diagram of the Electronic System

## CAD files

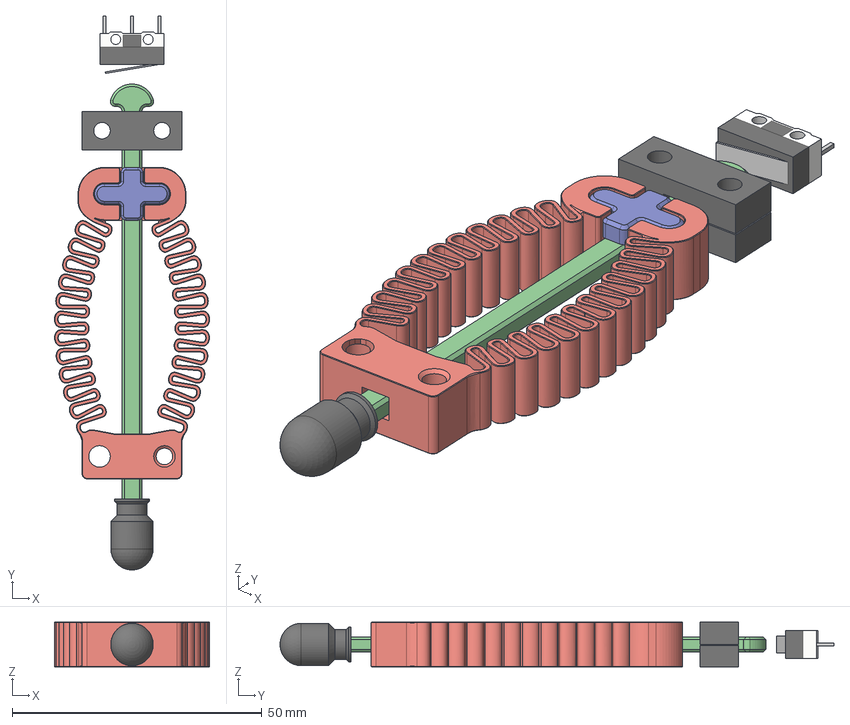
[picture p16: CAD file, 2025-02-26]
modele hex/Leg spring assembly v18.step
31.1 x 111.0 x 9.00 mm
endstop switch v1
spring
holder
TPU cap

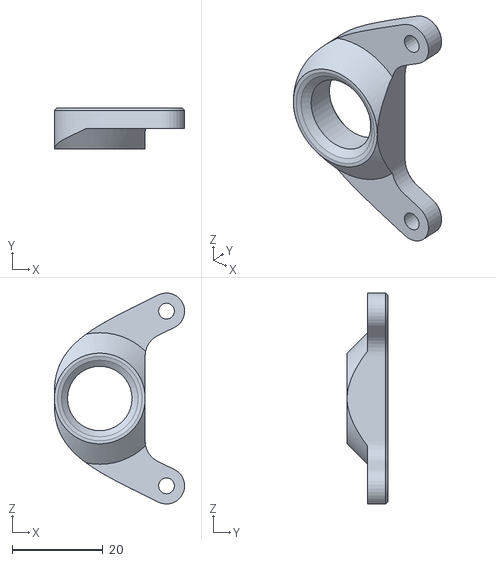
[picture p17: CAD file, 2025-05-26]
hardware/3D models printing/DRUKOWANIE PROTO/printing sesion 1 - mid section part 1/0.4 nozzle/Gearbox 3 Mount.stl
28.7 x 9.00 x 46.5

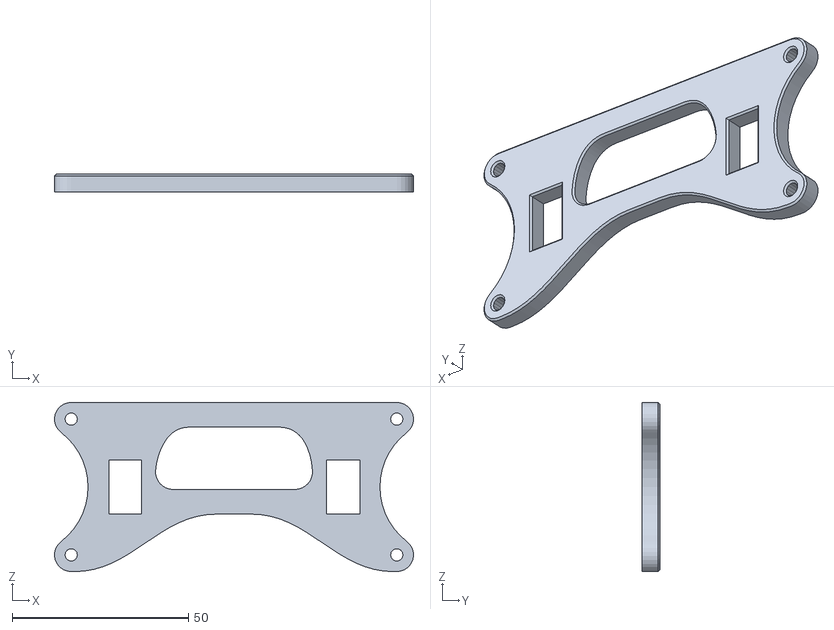
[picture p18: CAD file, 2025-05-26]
hardware/3D models printing/DRUKOWANIE PROTO/printing sesion 1 - mid section part 1/0.4 or 0.6 nozzle/Mid Section Truss Front.stl
101.9 x 5.00 x 48.0

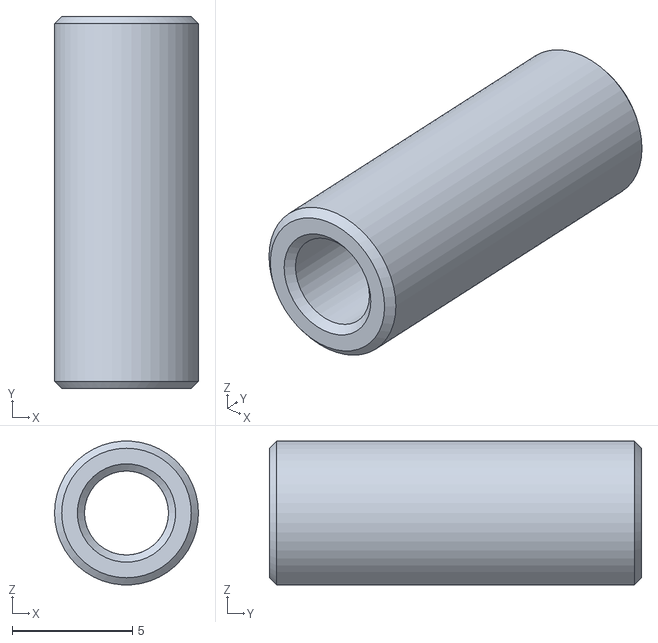
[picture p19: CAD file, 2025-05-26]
hardware/3D models printing/DRUKOWANIE PROTO/printing sesion 1 - mid section part 1/0.4 or 0.6 nozzle/mid section truss rod long (identyczne modele)/mst uf.stl
6.00 x 15.5 x 5.99

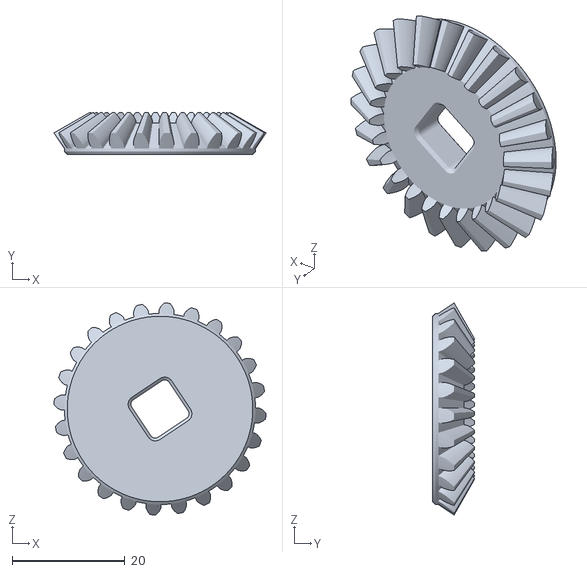
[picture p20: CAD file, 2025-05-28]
hardware/3D models printing/DRUKOWANIE PROTO/printing sesion 2 - mid section gears/0.4mm nozzle/bevel 24.stl
37.6 x 7.39 x 37.6

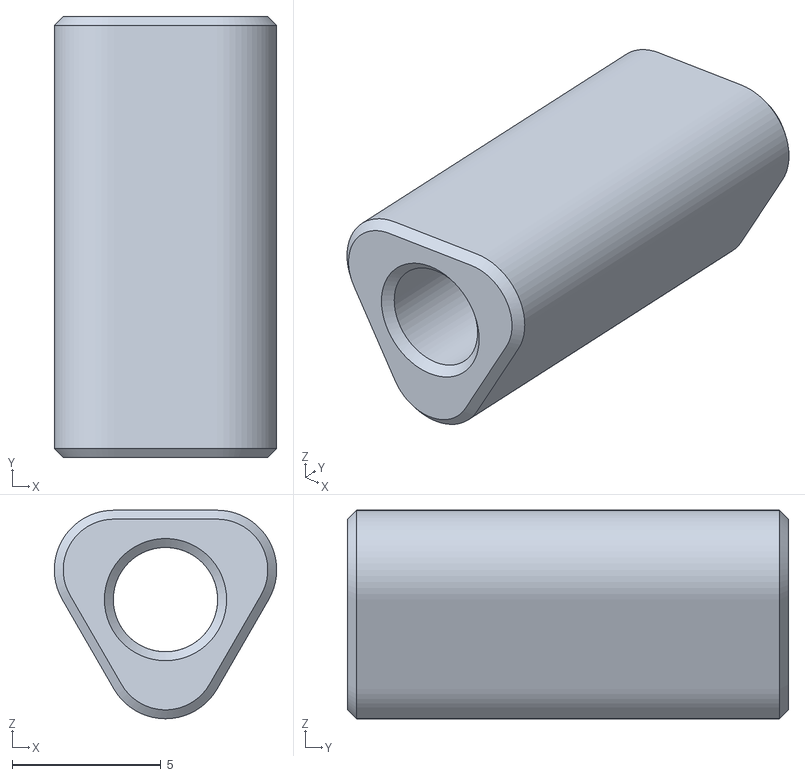
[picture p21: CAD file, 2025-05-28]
hardware/3D models printing/DRUKOWANIE PROTO/printing sesion 3 - down section truss/0.4mm or 0.6mm nozzle/ds dt.stl
7.46 x 14.8 x 7.00

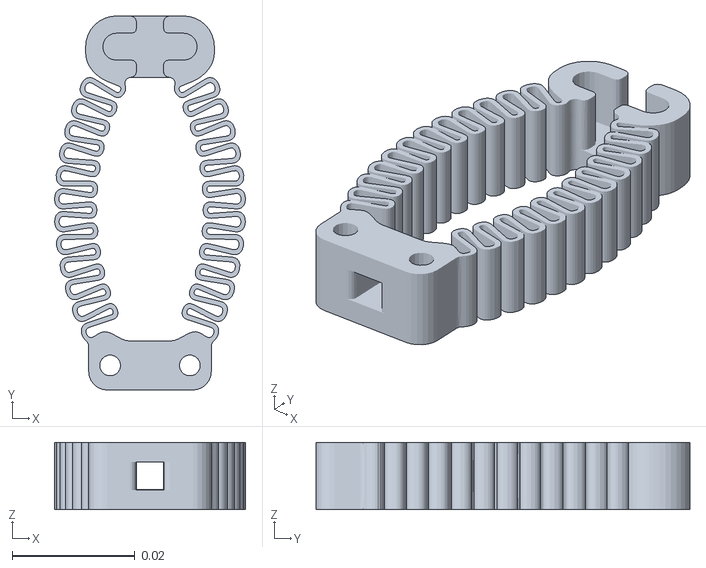
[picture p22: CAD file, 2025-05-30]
hardware/3D models printing/DRUKOWANIE PROTO/printing sesion 4 - down section spring assembly/0.4mm nozzle PETG red/Spring.stl
0.0312 x 0.061 x 0.011

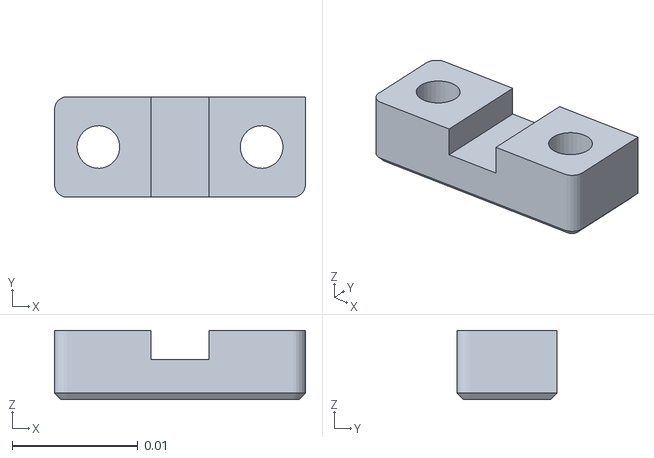
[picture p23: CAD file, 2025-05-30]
hardware/3D models printing/DRUKOWANIE PROTO/printing sesion 4 - down section spring assembly/0.4mm nozzle/rod holder back.stl
0.02 x 0.008 x 0.0055

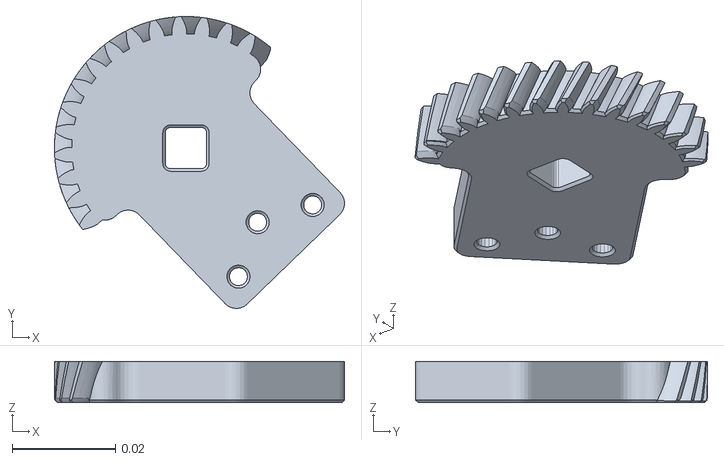
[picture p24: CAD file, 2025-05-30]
hardware/3D models printing/DRUKOWANIE PROTO/printing sesion 5 - top section/0.4mm nozzle/Spur 32.stl
0.0563 x 0.0566 x 0.008

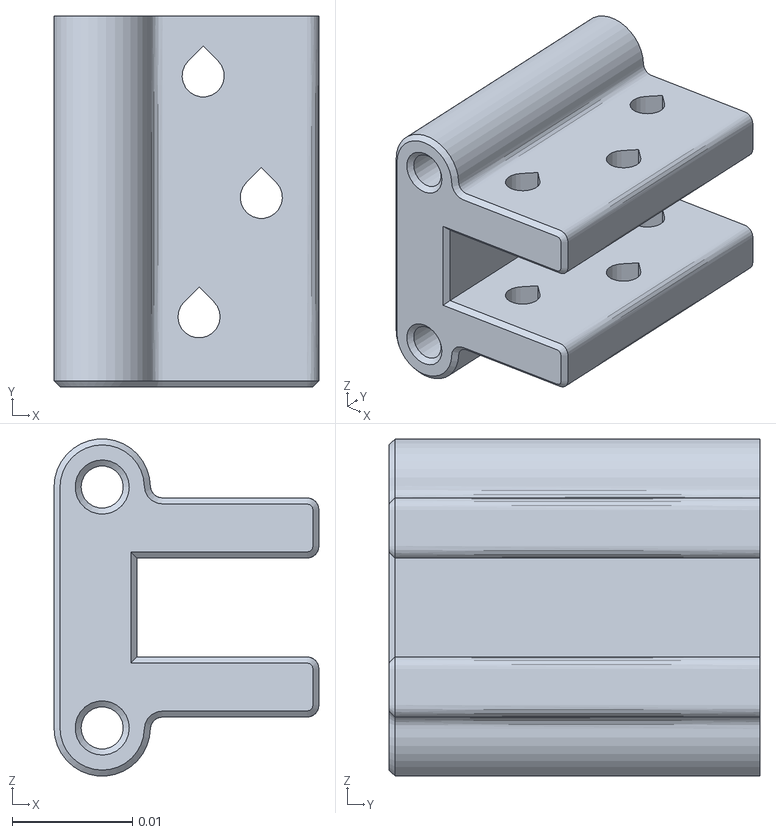
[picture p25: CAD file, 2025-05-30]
hardware/3D models printing/DRUKOWANIE PROTO/printing sesion 5 - top section/0.4mm or 0.6mm nozzle/Top Section Holder.stl
0.022 x 0.0308 x 0.028

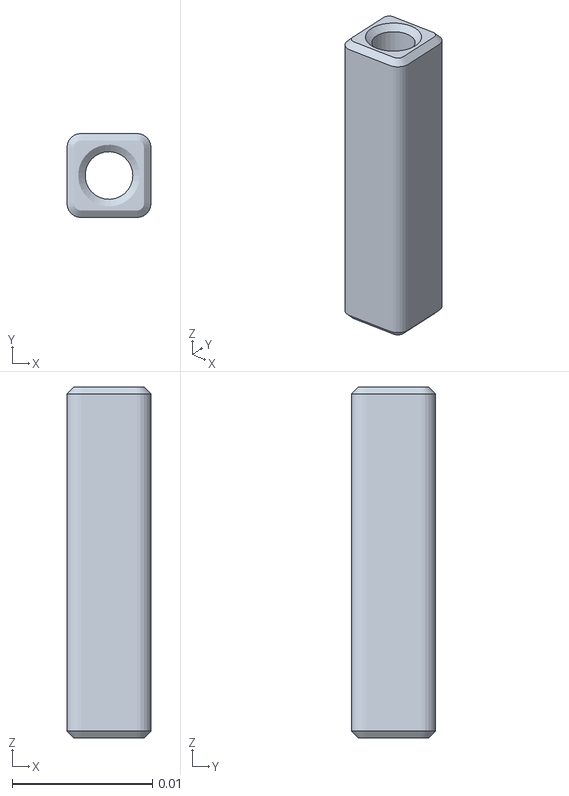
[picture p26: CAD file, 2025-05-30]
hardware/3D models printing/DRUKOWANIE PROTO/printing sesion 6 - hexapod platform/0.4mm nozzle/support rod.stl
0.006 x 0.006 x 0.025

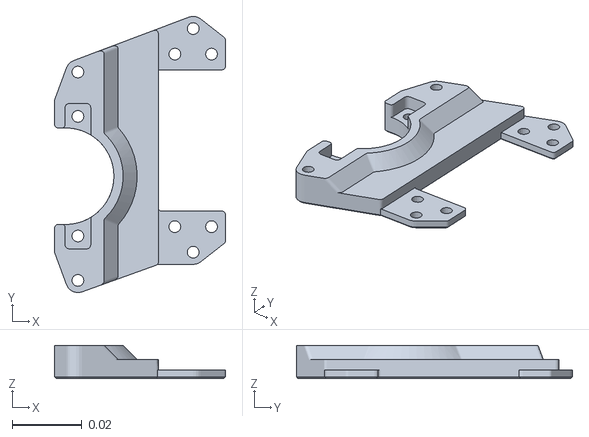
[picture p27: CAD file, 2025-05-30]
hardware/3D models printing/DRUKOWANIE PROTO/printing sesion 6 - hexapod platform/0.4mm or 0.6mm nozzle/bearing mount L4 down.stl
0.049 x 0.079 x 0.00955

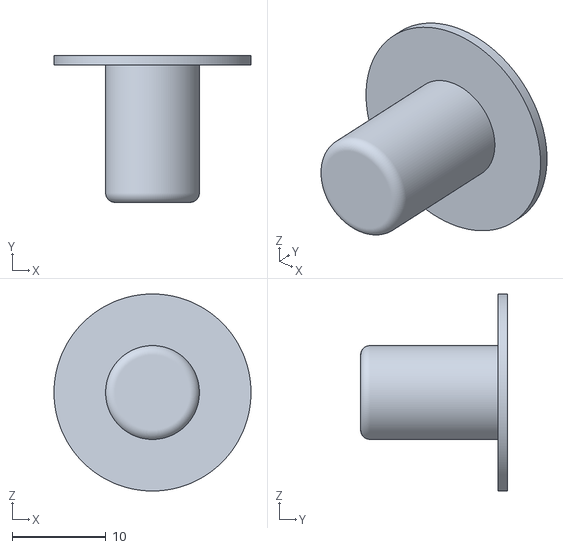
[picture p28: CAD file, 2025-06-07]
hardware/3D models printing/Silicon Cast Mold/Mold Stiff In.stl
21.0 x 15.6 x 21.0

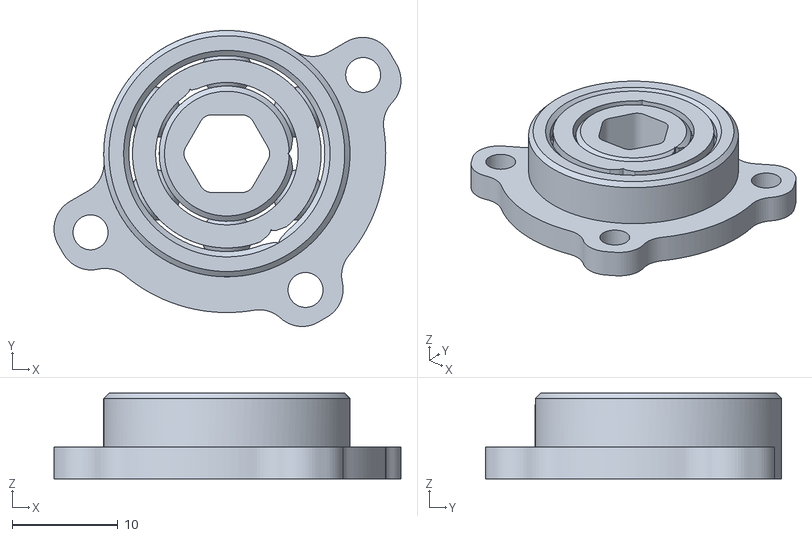
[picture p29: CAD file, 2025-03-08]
modele hex/Ball bearings/ball bearing 3_16''.stl
32.7 x 27.9 x 8.10

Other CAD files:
modele hex/hexapod leg/down section/bevel gear assembly/pinion 24.stl
modele hex/hexapod leg/down section/leg down section/rod 2.stl
modele hex/hexapod leg/down section/leg spring assembly/Linear Holder DWN.stl
modele hex/hexapod leg/mid section/bevel gear assembly/pinion 24.stl
hardware/3D models printing/DRUKOWANIE PROTO/printing sesion 1 - mid section part 1/0.4 nozzle/pinion 16.stl
hardware/3D models printing/DRUKOWANIE PROTO/printing sesion 1 - mid section part 1/0.4 nozzle/servo mount back.stl
hardware/3D models printing/DRUKOWANIE PROTO/printing sesion 1 - mid section part 1/0.4 nozzle/servo mount front.stl
hardware/3D models printing/DRUKOWANIE PROTO/printing sesion 1 - mid section part 1/0.4 or 0.6 nozzle/Mid Section Truss Back.stl
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

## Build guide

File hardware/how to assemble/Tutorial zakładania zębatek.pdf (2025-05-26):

# Tutorial zakładania zębatek

Opisany poniżej sposób zakładania zębatek pozwala na sztywny montaż zębatek do wału serva. Średnica wewnętrzna otworu w zębatce wynosi około 4,9mm , a średnica wału serva to: 5,9mm.

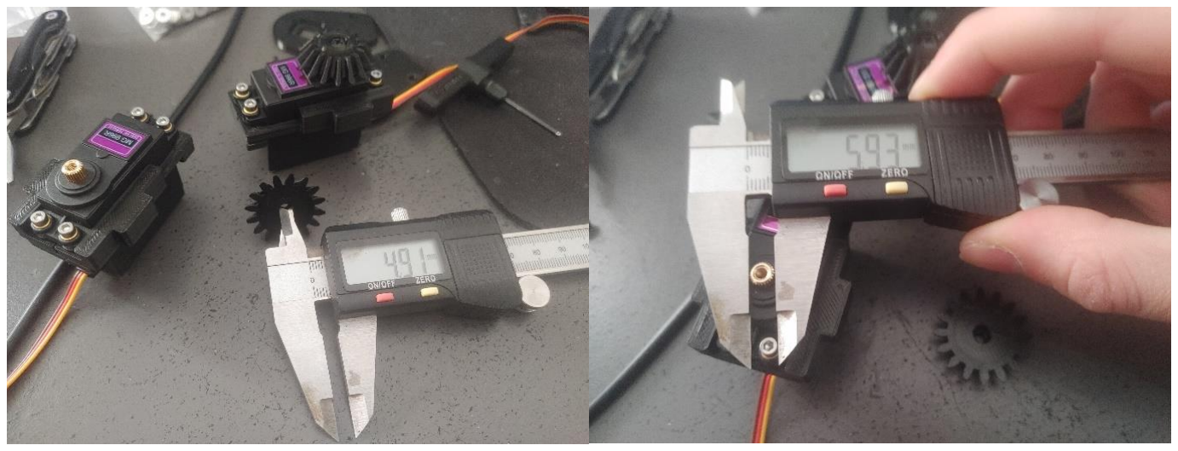
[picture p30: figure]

Otworu nie należy poszerzać! Zębatki nie należy zakładać na siłę!

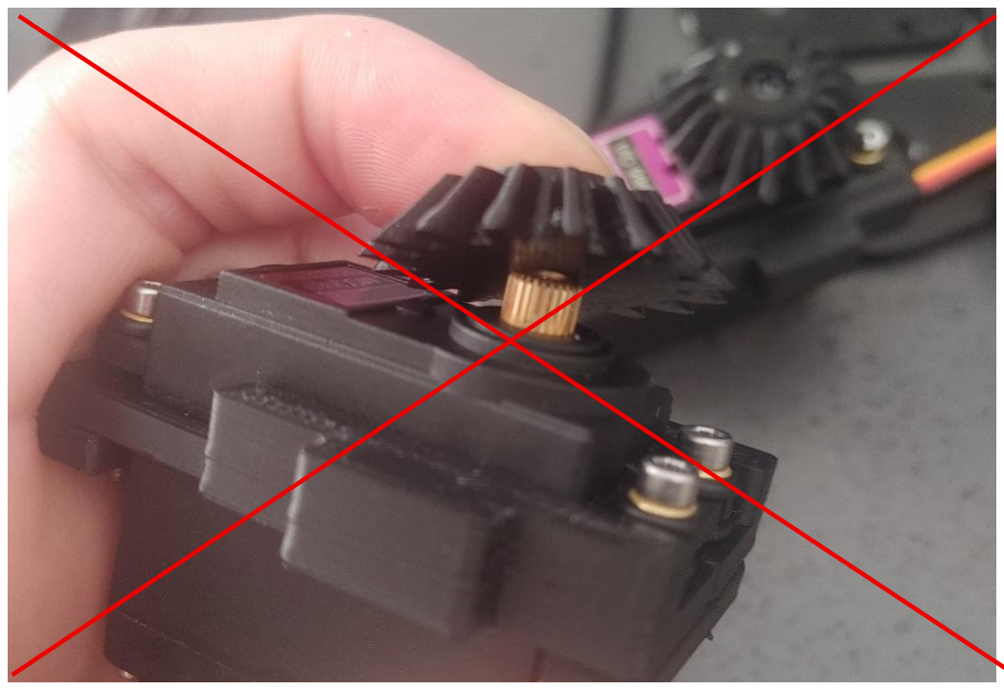
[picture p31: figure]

Dopasowanie otworu zębatki do wału następuje poprzez nagrzanie zębatki powyżej temperatury zeszklenia materiału (dla PLA Tg = 60°C). Dopasowany tak otwór zapewnia blokadę rotacyjnego stopnia swobody zębatki i zapobiega odkręcaniu się śruby.
Zębatkę można bez problemu ściągać z wału.

Nagrzej hotair do około 120°C, w tej temperaturze ciężko o oparzenia, co pozwala na zginanie PLA w dłoni:

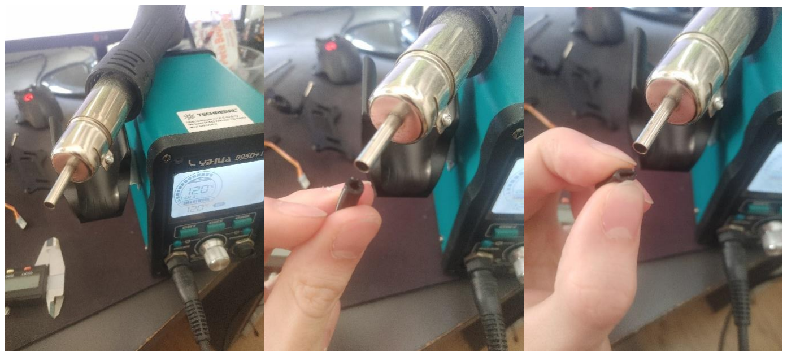
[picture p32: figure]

Przygotuj zębatkę i serwo, nagrzej otwór (nie za bardzo żeby nie stopić prowadnicy śruby, aczkolwiek tolerancja jest duża), szybko usuń serwo ze strumienia powietrza i wciśnij je na servo. Początkowo metalowy element serva będzie pochłaniał temperaturę z uwagi na duże przewodnictwo cieplne. Procedurę powtórz około 3 razy, tak aby servo można założyć do końca.
Nie nagrzewaj wału serva, bo je uszkodzisz!

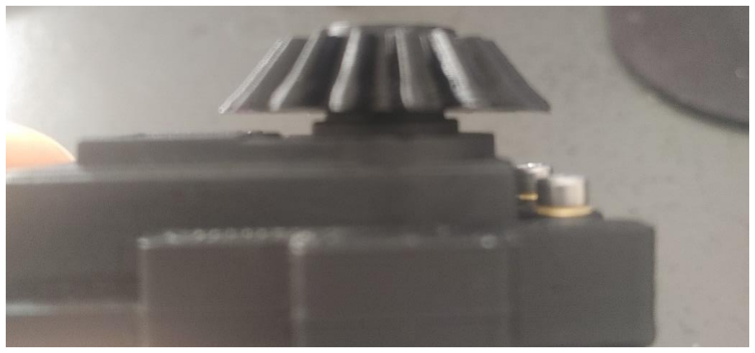
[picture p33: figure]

Zębatka ma małą powierzchnię styku z obudową serva, więc zastosowanie smaru nie jest konieczne!

Teraz wystarczy dokręcić śrubę i gotowe. Nie uszkodź gwintu!

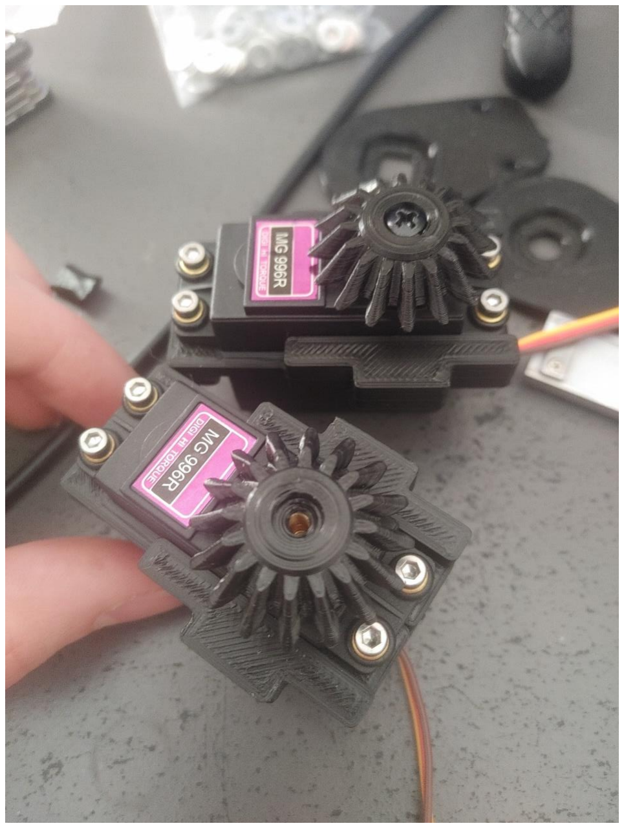
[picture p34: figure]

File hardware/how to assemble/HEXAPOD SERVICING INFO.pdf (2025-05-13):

## HEXAPOD SERVICING INFO

This document provides additional info for Hexapod assembly and servicing routines.

Servo gear mounting:
In order to properly secure the 3D printed gear to the servo shaft a strong adhesive is required, without this the mounting screw will loosen while rotating clockwise under high torque. This means that the gear can not be easily detached from the servo once installed.

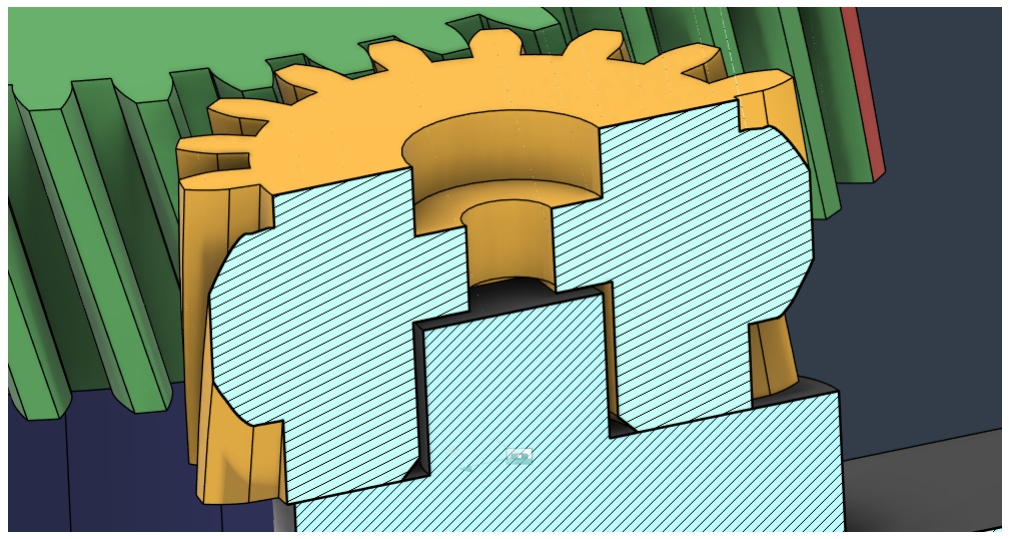
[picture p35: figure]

1. First apply grease on the horizontal interface surface between the servo and the gear. This prevents friction if the gear screw is overtightened, and prevents excess spill of glue from bonding with the servo case.
2. Apply a small amount of glue into the servo shaft, this step can be omitted if the tolerance between the gear hole and the shaft is tight.
3. Apply a small amount of glue on the 2mm kit bolt, firmly press down on the bolt when installing.

Bolting the parts together:
While securing the parts together with bolts make sure to use washers where possible and apply grease on the stainless still bolts. White DX Paste was used for bolts.

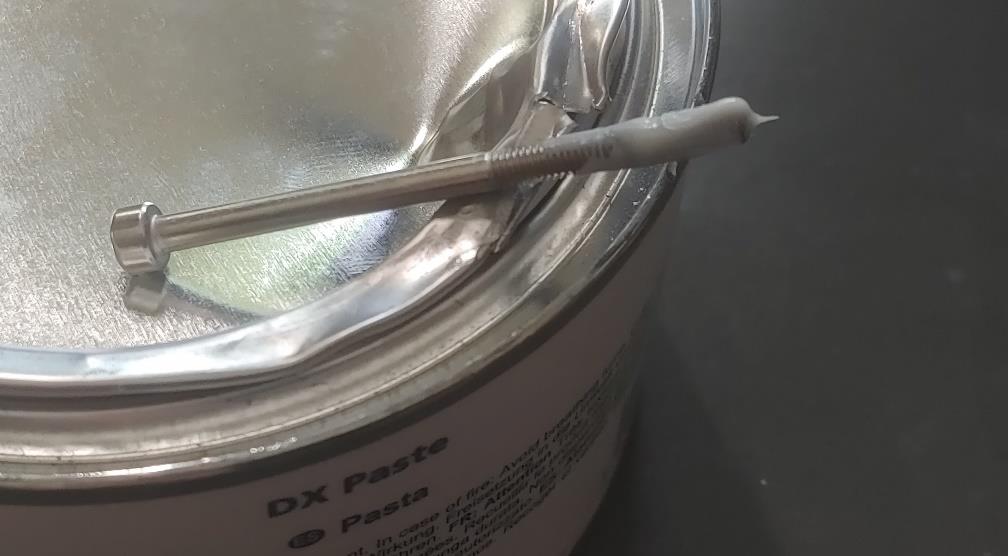
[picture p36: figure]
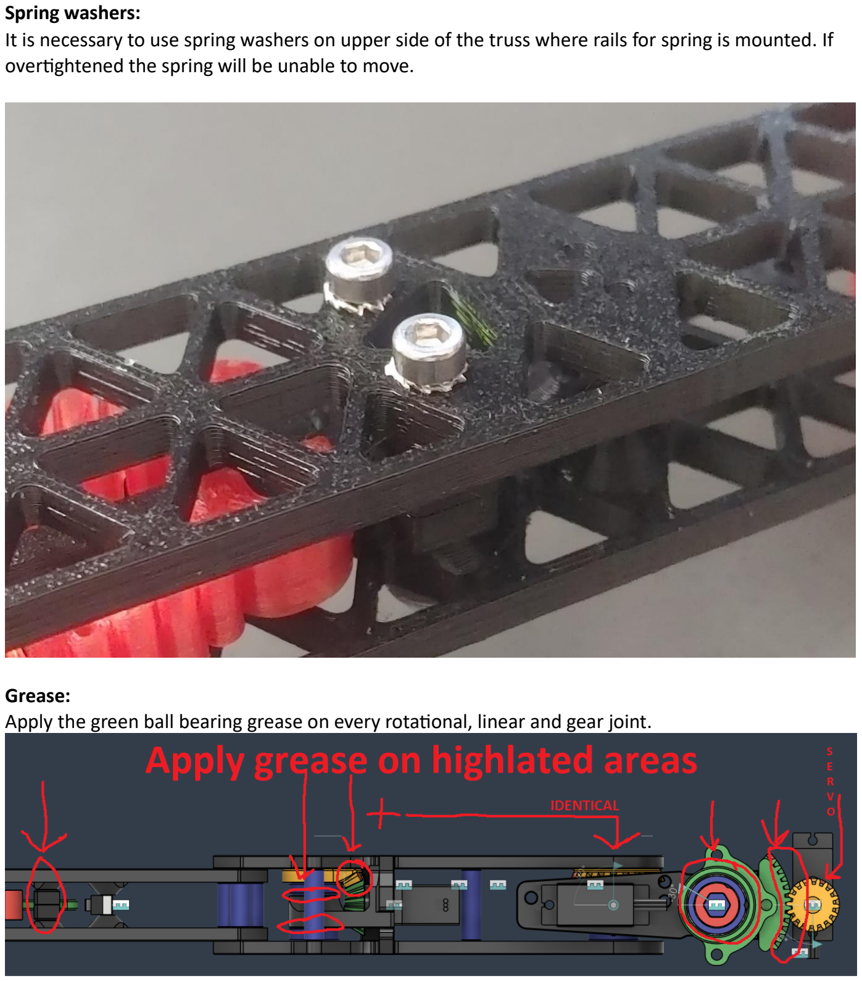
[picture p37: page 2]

Spring washers:
It is necessary to use spring washers on upper side of the truss where rails for spring is mounted. If overtightened the spring will be unable to move.

Grease:
Apply the green ball bearing grease on every rotational, linear and gear joint.

TPU end caps:
Secure the TPU end caps with a cable tie.

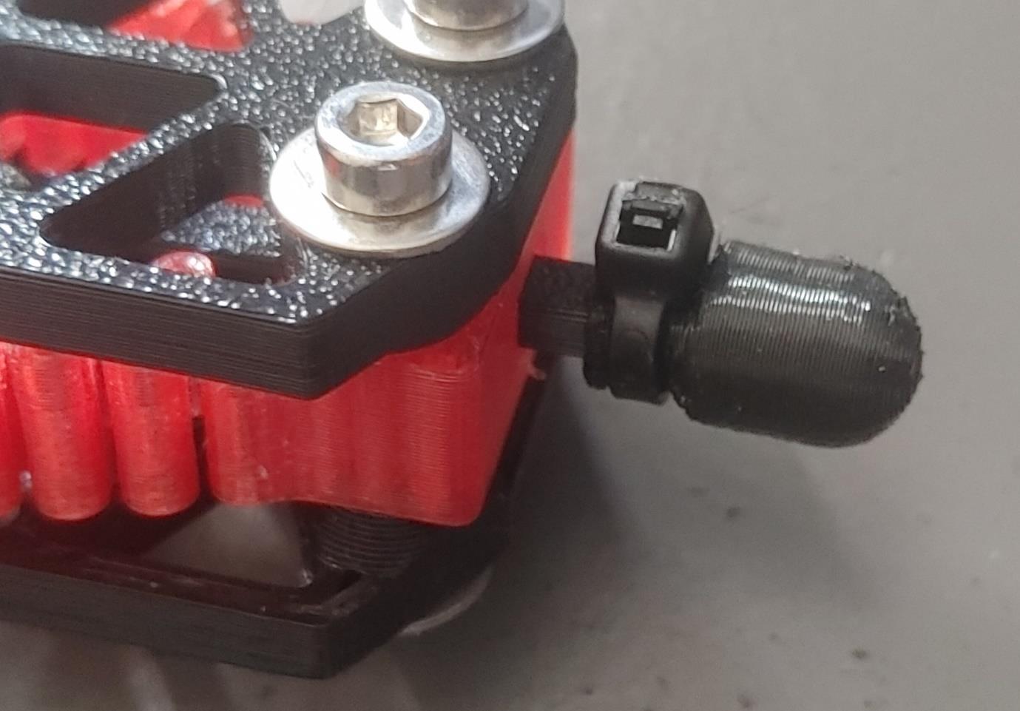
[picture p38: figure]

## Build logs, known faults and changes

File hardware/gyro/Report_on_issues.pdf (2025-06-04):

Trajectory Reconstruction Based on IMU Data - report

So far, we have relied on an algorithm combining data from 2 IMUs, which:
- used rotation matrices to determine accelerations in the global coordinate system
- performed noise filtering using Butterworth filters / alpha filters
Observed and potential problems:
- The current rotation method was based on Euler angles and rotation matrices, which could lead to Gimbal Lock - two axes become collinear. Consequently, this results in large jumps even with small changes in measurements. Potential solution: use quaternions instead of rotation matrices and Euler angles.
- Accumulation of errors resulting from double integration (acceleration -> velocity -> position) seems inevitable if we rely solely on IMU data.
- So far, thresholds for when the robot is considered stationary have been manually set based on observations, which could lead to ignoring useful data.
- Using a Kalman filter can yield better results but requires knowledge of the object model, which seems difficult to obtain, if at all possible, since the robot will have many walking modes.
Madgwick and Mahony filters allow reconstructing orientation based on IMU data, but unfortunately, they are unlikely to help much with position. However, they may be useful for determining whether the robot is walking on a flat surface or not: http://www.cs.ndsu.nodak.edu/~siludwig/Publish/papers/SPIE20181.pdfhttp://wiki.ros.org/imu_filter_madgwick

Factor graph optimization may prove useful and requires testing.

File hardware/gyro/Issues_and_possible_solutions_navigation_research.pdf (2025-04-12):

## Issues and possible solutions

The current challenges stem from the fact that obtaining positions requires the double integration of acceleration, a process that inherently promotes the accumulation of errors. An additional source of error is the noise detected by the IMU. As demonstrated in the following video https://www.youtube.com/watch?v=C7JQ7Rpwn2k 23:21 , simple filtering—for example, using a low-pass filter—is insufficient to solve this problem.

More sophisticated solutions are necessary, such as implementing a Kalman filter or integrating data from a larger number of sensors (e.g., a magnetometer), as proposed in the report: https://www.cl.cam.ac.uk//techreports/UCAM-CL-TR-696.pdf This report focuses specifically on the errors in navigation based on accelerometers and gyroscopes and may prove valuable in subsequent stages.

If we decided to use a Kalman filter for example, it would be needed to create specific model of movement of IMU on the hexapod which seems to be quite hard

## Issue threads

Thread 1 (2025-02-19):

Design of mechanical construction

Siedmiu, 2025-02-19:
Design of adjustable 3D model with mechanical links.
- [x] Gears
- [x] Gear assembly
- [x] Servo holders
- [x] Leg assembly

Closed 2025-03-07.

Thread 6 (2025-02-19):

Microcontroller Research

Siedmiu, 2025-02-19:
Determine the right microcontroller for the job.
It has to work with the servo controller and be sufficient for the calculations.
Contact other teams for the specifics.
(this task will be available when Założenia projektowe are clarified)

Consider:
- price
- ease of use
- GPIO pins
- ...

NatanTulo, 2025-03-09:
## Choosing the Best SoC

On the [Espressif site](https://products.espressif.com/static/Espressif%20SoC%20Product%20Portfolio.pdf), there is an **Espressif SoC Product Portfolio** document that compares all available ESP32 family chips.

In the **HMI** section, there is a "Camera Interface" feature, which will be useful for gesture control. This requirement significantly narrows down the available options.
Moreover, we need **WiFi connectivity** to communicate between our Android app and the hexapod while also streaming a live camera feed.

Given these requirements, three microcontrollers remain:
1. The **original ESP32** (default, older version).
2. The **ESP32-S series**, which is newer and faster.

For development purposes, a more capable SoC is preferable, so **ESP32-S3** appears to be the best option. It's also **dual-core**, so, for example, one core could handle camera streaming while the other independently controls the hexapod’s servos based on incoming commands.

FlyBozon, 2025-03-09:
Using an **ESP32-S3** is possible, but it would require **offloading all computations to the Android app**, meaning the app must handle **inverse kinematics, gait generation, and motion planning**, while the ESP32 acts as a **communication bridge and servo controller**.

#### **Challenges & Possible Solutions**

1. **Latency Issues** (WebSocket delays: **20-100ms** on local networks) → Can cause **jerky movement** if gait updates are not frequent enough.
   - **Solution:** Implement **prediction-based motion smoothing** on ESP32 (for that we should find/create a specific algorithm and implement, maybe somehow test it already now, to be sure that it would work).

2. **Synchronization Problems** (Inconsistent app command timing) → May lead to unstable walking patterns.
   - **Solution:** Use **timed execution loops** on ESP32 to interpolate between received commands smoothly.

3️3. **ESP32 Processing Limitations** → If ESP32 needs to handle minor calculations (e.g., PID control for smoother walking), we must ensure it does not introduce further delays.
   - **Solution:** Consider **Micro-ROS on ESP32** to integrate better with ROS2 (needs testing before committing to this approach).

#### **Next Steps & Considerations**

- **Option 1:** Fully rely on **ESP32 + Android app** (but risks latency issues).
- **Option 2:** Use ESP32 **only for low-level servo control** and add a secondary controller like **STM32 or RPi** for real-time processing (higher cost but potentially more reliable) OR just use STM32/PRI, but better firstly try cheaper options.
- **Testing Plan:** Since an ESP32-S3 is available, testing **WebSocket latency, motion smoothing, and Micro-ROS feasibility** will help decide the best approach before purchasing additional hardware.

FlyBozon, 2025-03-09:
Jednak, z przybliżeniem inżynierskim, można pójść w ESP32, a jeżeli pojawią się problemy, to wtedy zastanowić się, co zrobić dalej :D

Siedmiu, 2025-03-09:
Ja szczerze mówiac nie jestem fanem obliczenia ruchu na telefonie, myślałem bardziej o wyznaczaniu ścierzek i wysyłaniu komend z temefonu a pająk niech steruje sobą (no i wszystko z obrazem na telefonie). Jak będziemy chcieli dosłowinie wszystko liczyć na telefonie to będzie bardzo dużo problemów. Po pierwsze jak uwzględnić sygnał zwrotny z przełączników krańcowych? W przewidywanie nie ma co się bawić, mma wrażenie że pełno problemów z tym będzie i dużo czasu zajmnie.

NatanTulo, 2025-03-09:
Nie wiem jak z poziomu ROSa, ale z poziomu apki w telefonie to nie ma różnicy czy się wyśle websocketa "idź do przodu" czy "rusz tym silnikiem o dokładnie tyle"

NatanTulo, 2025-03-09:
Jedynie obstawiam że problematyczne może być połączenie dwóch rozwiązań na jednym mikrokontrolerze, czyli jednocześnie streaming obrazu oraz Micro-ROS, więc można wtedy alternatywnie poszukać innego rozwiązania do obsługi kamery - może już nie na bazie ESPa a czegoś bardziej dedykowanego

Siedmiu, 2025-03-09:
Najlepsze rozwiązanie to będzie coś pomiędzy najtańszyma a najprostszym. W sumie to nie musimy obrazu i sterowania robić na jednym MK. Teraz pytanie czy coś dedykowane do kamery będzie potrzebne, czy może po porstu dać drugiego ESPa z kamerą.

NatanTulo, 2025-03-09:
## Which Board Exactly Do We Want?

Important aspects to consider:
1. **Built-in 24-pin camera connector** – This makes it easier to use a camera without designing an entire PCB for it.
2. **Full-sized board with as many GPIOs as possible** – We will need them for IMUs, encoders, and other sensors.
3. **Memory versions** – For example, the **N16R8** version means **16 MB of FLASH** and **8 MB of PSRAM**. I’m not sure how much we need, but having some reserve is better than running out.
4. **External antenna?** – It’s good to have the option in case the built-in one isn’t sufficient.

## ESP32-S3 Boards Available in Local Stores

### **Seeed XIAO ESP32-S3 Sense**
- [Botland (80 PLN)](https://botland.com.pl/moduly-wifi-i-bt-esp32/22926-seeed-xiao-esp32-s3-sense-zestaw-z-kamera-ov2640-wifibluetooth-seeedstudio-113991115.html)
- [Kamami (70 PLN)](https://kamami.pl/xiao/1185392-xiao-esp32s3-sense-plytka-z-modulem-wifi-i-ble-esp32-s3-oraz-kamera-i-mikrofonem-5906623414970.html)
- [Mouser (57 PLN, but 80 PLN shipping unless >200 PLN order)](https://www.mouser.pl/ProductDetail/Seeed-Studio/113991115?qs=3Rah4i%252BhyCEkFZeikDKazg%3D%3D)

📌 **Advantage:** Has an **SMA connector for an external antenna**, which might be useful if the built-in one isn’t sufficient.
📌 **Issue:** Limited number of GPIOs, which we need for sensors.

---

### **FireBeetle 2 ESP32-S3-U (PCB Antenna, N16R8)**
- [Botland (99 PLN)](https://botland.com.pl/plytki-zgodne-z-arduino-dfrobot/23330-firebeetle-2-esp32-s3-u-wifi-bluetooth-kamera-ov2640-dfrobot-dfr0975-6959420923403.html)
- [Kamami (97 PLN)](https://kamami.pl/firebeetle/1186679-firebeetle-2-plytka-rozwojowa-z-esp32-s3-i-kamera-ov2640-modul-na-plytce-5906623407637.html)
- [Mouser (81 PLN, but 80 PLN shipping unless >200 PLN order)](https://www.mouser.pl/ProductDetail/DFRobot/DFR0975?qs=17ckDYBRdemkx10aE%252B0XGw%3D%3D)

📌 **Issue:** No external antenna.

---

### **FireBeetle 2 ESP32-S3-U (External Antenna, N16R8)**
- [Botland (109 PLN)](https://botland.com.pl/plytki-zgodne-z-arduino-dfrobot/23329-firebeetle-2-esp32-s3-u-wifi-bluetooth-zewnetrzna-antena-kamera-ov2640-dfrobot-dfr0975-u-6959420923397.h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)
- [Kamami (99 PLN)](https://kamami.pl/firebeetle/1186678-firebeetle-2-plytka-rozwojowa-z-esp32-s3-i-kamera-ov2640-antena-zewnetrzna-5906623407620.html)
- [Mouser (85 PLN, but 80 PLN shipping unless >200 PLN order)](https://www.mouser.pl/ProductDetail/DFRobot/DFR0975-U?qs=17ckDYBRdek%252BKZ3fyFofFQ%3D%3D)

📌 **Advantage:** Has an **SMA connector for an external antenna**, which might be useful if the built-in one isn’t sufficient.

## ESP32-S3 Boards Available on AliExpress

### **ESP32-S3 with 8 MB PSRAM**
- [AliExpress (34 PLN)](https://pl.aliexpress.com/item/1005007495876281.html) – 46 sold, no external antenna.

### **ESP32-S3 with 8 MB PSRAM**
- [AliExpress (31 PLN)](https://pl.aliexpress.com/item/1005007308040075.html) – 231 sold, also no external antenna.

### **ESP32-S3 WROOM N16R8 CAM (GOOUUU CAM)**
- [AliExpress (40 PLN)](https://pl.aliexpress.com/item/1005007544932625.html) – 500+ sold, well-documented on [Github](https://github.com/zhuhai-esp/ESP32-S3-Goouuu-Cam/tree/main).
  📌 **Tested** – Bought for 30 PLN a bit over a month ago, works well.
  📌 **Extras** – Built-in **RGB LED** (could be useful for status signaling), has an **SMA connector** for an external antenna.

FlyBozon, 2025-03-09:
Znaczy, do przetwarzania obrazu ESP nadaje się i jest wystarczający (bardziej do przesyłania na Androida, bo z przetwarzaniem i wykrywaniem obiektów będzie ciężko). Ale już to połączenie z ROS-em... ROS sam w sobie jest za ciężki dla ESP, ewentualnie jest micro-ROS, ale trochę zredukowany i i tak będzie ciężko, ale jakoś będzie (bez ć). Inna opcja to znaleźć RPi do tego ROS-a i wtedy nie ma problemu ani kombinowania

Closed 2025-03-13.

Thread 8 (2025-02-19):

BOM

FlyBozon, 2025-02-19:
**Parts List for the Project**

Initial estimate:

- 24 servo motors (3x6 + 6) (e.g. MG996R)
- Control board (ESP32/STM32)
- Servo driver board (1 or 2, depending on outputs) (e.g., PCA9685)
- Plastic + other materials for physical construction (3D printed/aluminum/acrylic)
- Camera module (ESP32-CAM / Raspberry Pi Camera)
- Power supply (Li-Po battery + voltage regulators)
- IMU sensor (MPU6050/MPU9250)
- Wireless module (Wi-Fi/Bluetooth/NRF24L01)
- Screws, standoffs, connectors, wiring
- Etc.

GOTO issues microcontroller and electronics research + contact @Siedmiu for details about design of mechanical construction

Siedmiu, 2025-03-09:
Current screw requirements after completing the platform and the ball bearing mounts are:
LEG (one):
- 6x M3 35mm
- 5x M3 25mm
- 3x M3 15mm
- 2x M3 10mm
- 4x M2,5 10mm
- 2x M2 25mmm
- plus nuts and washers for each screw

PLATFORM (no electronics yet):
- 8x M3 40mm
- 18x M3 20mm
- 22x M3 15mm
- 12x M2,5 15mm
- plus nuts and washers for each screw

I didn't restrict myself to standard screw lengths so rounded cap nuts may be nice.

Siedmiu, 2025-03-09:
Gyroscope + accelerometer module ~10zł
https://randomnerdtutorials.com/esp32-mpu-6050-accelerometer-gyroscope-arduino/
https://allegro.pl/oferta/modul-mpu-6050-zyroskop-gy-521-akcelerometr-3-osiowy-axis-do-arduino-rc-10018953998

Siedmiu, 2025-03-12:
Tuż przed zakupem ktoś wykupił jedno z sterowników serw, więc musiałem szukać gdzie indziej, tak się składa że znalazłem taniej. Z elektrowebu resztę zamówiłem z allegro bo mam darmową wysyłkę.
Najważniejsze rzeczy zamówione, Miłosz może po taniości załatwi nam baterie z firmy. Ogólnie to w 500zł się nie zmieścimy ale będzie całkiem blisko.

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

Siedmiu, 2025-03-12:
Obecnie wydane 444.40 zł. Potrzeba jeszcze zasilania, śróbek i kabli.

JuliaHry, 2025-03-14:
Wydaje mi się, że się zgadza

Siedmiu, 2025-03-14:
Update, zasilacz

[PRZETARG NA CZĘŚCI.pdf](https://github.com/user-attachments/files/19252792/PRZETARG.NA.CZESCI.pdf)

Closed 2025-05-31.

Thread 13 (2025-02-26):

Inverse Kinematics Equations

Siedmiu, 2025-02-26:
Calculate inverse kinematics equations for the Hexapod robot.

Bonk03, 2025-05-05:
Final version is ready!!!

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

I changed full calculations to take into account the displacement of joints relative to each other and redefine alfa_3 to be equal to alfa_3 used in simulation

Bonk03, 2025-05-09:
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
well, i had to change minus in joint 2, hope it is final version now XD

Bonk03, 2025-06-12:
finall using ofinverse kinematics

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

Closed 2025-03-08.

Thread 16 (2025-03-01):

Walking Algorythms Simulation

Siedmiu, 2025-03-01:
@Bonk03 and @JuliaHry have decided that they are going to continue the Walking Algorythm Research #11 task by creating a visual animation using Python.

Bonk03, 2025-03-08:
to move legs with constant velocity in first stage we have to calculate points that have same lenght of function between them instead of same lenght between w coordinates like in the second stage of movement. So it can be like that (green) and not like that (red)

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

Bonk03, 2025-03-08:
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
I calculated track of a movement for each leg based on a  of points we wnat on a line and the angle at which the leg is tilted relative to the robot's center coordinate system

Bonk03, 2025-03-08:
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
For example for leg 1 has to move forawrd in direction x and y of a leg to move whole hexapod only in y coordinates

Bonk03, 2025-03-12:
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

Leg cycle for legs 1, 3, 5 goes : 1, loop(2, 3, 4), 2, 3, 5
Leg cycle for legs 2, 4, 6 goes : 3, loop(4, 2, 3), 4, 2

Every stage has got the same number of points exept 4th stage it has got 2 * number of points

full leg cycle for legs 1, 3, 5looks like that:

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

full leg cycle for legs 2, 4, 6 looks like that:

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

Bonk03, 2025-03-15:
> 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 So, these are my calculations on how leg has to move its feet relative to the center of hexapod if we want to make it rotate around its own axis
>
> Nogi 1 : 1, 3, 4, 6 Nogi 2 : 2, 5 gamma : inclination R relative to the horizontal axis of the robot center reference system beta: inclination of the robot leg relative to the horizontal axis of the robot center reference system

So, I didn't think here about rotation of the coordinate system relative to the leg, when whole hexapod is rotating. I calculated coordinates in right way but in old coordinate system(beforem movement). I think that we have to take this into account and I will make calculations for it again. Sorry....

Bonk03, 2025-03-15:
update for legs 2 and 5

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

Bonk03, 2025-03-15:
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
For other legs

Bonk03, 2025-03-15:
OK, so what i calculated is a cycle for legs 2 and 5 to rotate with constant angle. It has to move like that in a cycle:

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

So, full rotation will be 2 * alpha * (1 + num_of_cycles)

Bonk03, 2025-03-15:
I got a problem with legs 1, 3, 4, 6, because I can't figure out how to move them after first movement

Bonk03, 2025-03-15:
OK, I think it will work the same for 1, 3, 4, 6
4 and 6 will go in a cycle with 2
1 and 3 will go in a cycle with 5
BUT x1 and x0 for them isn't equal to x0 and x1 for legs 2 and 5

Bonk03, 2025-03-16:
Today I counted these algorithms on paper to find out if they are accurate and results were equal to the truth

> 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 For other legs

Bonk03, 2025-03-23:
Well, I forgot to check if the clockwise turn works... it doesn't. So I had to do math to make calculations how leg change turning clockwise. I assumed that the angle by which we want the hexapod to rotate during one cycle of rotation around itself is less than 90 to make the accuracy of the rotation satisfactory and I did not take into account the cases of sudden angles of rotation greater than 90 degrees!!!

Bonk03, 2025-03-23:
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
it is only for clockwise turns!!!

Bonk03, 2025-03-23:
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

For hexapod rotating around itself cycle is a little bit shorter, to make higher accuracy of angle rotation:
Leg cycle for legs 1, 3, 5 goes : 1, loop(2, 3, 4), 2
Leg cycle for legs 2, 4, 6 goes : 3, loop(4, 2, 3), 5

Bonk03, 2025-03-24:
Movement of each leg during counter clockwise rotation:

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

Movement of each leg during clockwise rotation:

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

pictures are from rotation_around_itself.py

Bonk03, 2025-05-27:
As I was working on algorythm to turn, for the first time I looked at parameters fo new model and I think I can do many simplifications, because every leg is equal, for legs 1 3 4 6 beta and fi angle is 45 degree and each leg has first joint in the same distance from middle of hexapod, so now hexapod looks something like that and now it will be way easier to rotate because it will be like rotating circle

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

Siedmiu, 2025-05-31:
This is a great thread and will be used in the documentation in the future.
All basic algorithms are currently finished. So I am marking this issue as complete.

New algorithms regarding traversing difficult terrain and sloped surfaces will be documented in a new issue.

Closed 2025-05-31.

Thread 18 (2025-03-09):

Research Navigation with ROS2&Gz

FlyBozon, 2025-03-09:
### **Description:**
Explore and document different **navigation approaches** for a hexapod robot using **ROS 2 Jazzy** and **Gazebo (GZ) Harmonic**. Identify suitable algorithms, tools, and packages for **localization, mapping, path planning, and obstacle avoidance**

FlyBozon, 2025-03-12:
**Mega short summary on ROS2 based navigation:**

Perception → Sensors provide data.
Localization → The robot determines its position.
Mapping → The environment is understood.
Path Planning → A safe route is calculated.
Obstacle Avoidance → Adjusts path dynamically.
Control & Execution → Robot follows the planned route.

**Scheme**
Create map -> localize yourself on the map -> select goal point -> use some algorithms to create routh -> <loop> GO -> check if everything goes fine -> correct yourself </loop>

_long version is available on repo_

FlyBozon, 2025-03-12:
**list of interesting articles on that topic:**

https://automaticaddison.com/building-a-map-of-the-environment-using-slam-ros-2-jazzy/
https://automaticaddison.com/autonomous-navigation-for-a-mobile-robot-using-ros-2-jazzy/

Closed 2025-03-12.

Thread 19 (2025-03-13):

Walking Algorythm Blending

Siedmiu, 2025-03-13:
@Bonk03 and @JuliaHry have already created gait cycles for the robot, which are our building blocks for more diverse movement.
One of the most complicated problems in our movement kinematics is blending them together. You have to figure out how to transition between the movements (this is the easier part), and how to make micro adjustment to the walk cycle to be able to follow curved lines.
Until #MISSING_ISSUE is complete use 0.1*x*sin(0.05x) as a test path.

Bonk03, 2025-03-23:
I was able to count the trajectory of the leg movement it needs to make to get from point A to B by passing through the selected peak point. I tried to work on a paraboloid intersected by a plane common to the points, nothing made sense to me, there were cases in which what I calculated did not make sense. Finally, I came up with the idea of parametrizing the function of each variable x, y, z so that when opbuting one variable does not affect the other. This works exactly as I planned. The code is uploaded to moving_codes, 3D_points_of_movement.py. I think we will be able to use this once we have determined the points where the legs should hit in order for the spider to move along the curve.

Siedmiu, 2025-03-27:
I tried, but didn't succeed. Implementation of ripple gate might be impossible for curved paths (maybe smooth ones will work). Wave gate might be the best for it because it minimizes the chance of leg colisions.
There are 2 approaches I tested, add micro adjustments of goal leg positions based on the path, or a better approach to transform the robot coordinate system so that it is alligned with tangent and normal of the curved path at each sampling point.
There is also a problem with keeping the static legs "glued" to the ground as the robot will pass through many singularity points.
I found a path planning chart for this in a research paper:
1. Pre defined required body path
2.finds foots 1-6 start positions
3. Calculate each leg stance phase path points to achieve the required body path
4. Check if the stability at each point along the path. NO -> go to 7, YES -> go to 5
5. Calculate each leg inverse kinematics
6. Check the legs kinematics limitations NO -> go to 7, YES go to 3
7. Each leg joints Path

Bonk03, 2025-03-31:
I calculated how leg has to move to rotate hexapod and move it at the same time. Code is in project. I only checked it on one example. I will see if other examples works.

Bonk03, 2025-04-02:
Other example:

P = (0,0)
delta x = 1
delta y = -2
N = (-2, 4)
A = N + (-6, 3)

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
geogebra results:

h = x = 4.8668850910106
i = -y => y = -6.8397869778364

python results:
x = 4.8668850910105546
y = -6.83978697783636

Bonk03, 2025-04-02:
I think this will be the last example that I uppload here, every option works fine.

P = (0,0)
delta x = -3
delta y = -1
N = (5, 0)
A = N + (3, 0)
alfa = 45 deg

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
geogebra results:

h = x = 3.4852813742386
i = -y => y = -7.0710678118655

python results:
x = 3.4852813742385718
y = -7.0710678118654755

Siedmiu, 2025-05-31:
Extensive work regarding the algorithms and their parametrisation has been conducted. The results are yet to be tested thoroughly on the new physical implementation.
Simulated robots can prepare their leg positions for the walk cycles.

This issue is potentially going to be revisited in phase 2 of the project where smooth pathing will be researched.

Current implementation is satisfactory and the issue is marked as done and closed.

Bonk03, 2025-06-02:
my commits for this issue:
739441f
f52e8d3

JuliaHry, 2025-06-02:
My commits for this issue:
1349058202997ed431ca868a2fa2bd06480c6453
da03ac1539995f1b148094c944f2b53d9ae5ee28

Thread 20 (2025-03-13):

Walking Algorythm Path Generator

Siedmiu, 2025-03-13:
Implement algorithms to create paths out of given points - Catmull-Rom Splines; B-Splines or Bezier curves.

Create a separate optimisation based method aimed to reduce the energy needed for hexapod to travel. Create a cost function based on curvature penalty, smoothness, length and proximity to the points.

Siedmiu, 2025-03-13:
The basic approach would be to traverse the path between the points in a straight line and rotate in place. The use of splines is going to allow us to merge the rotation and movement, allowing us to conserve energy and traverse the path faster.

Catmull-Rom spline is a c1 continuity spline, it would be the easiest to calculate, but it is similar in operation to connecting the points with straight lines.

B-Splines have c2 continuity with local control, but they don't interpolate most control points. The motion path is very smooth, and it is located inside the convex haul of the points.

Siedmiu, 2025-03-13:
Natural Cubic Splines seem to be the best for our use case. They naturally minimise the acceleration along the path and interpolate all of the points (c2 continuity but no local control). They are less complex than B-splines. Each section needs to solve 8x8 matrix equation.
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

Sources:
Graphics in 5 minutes spline series: https://youtu.be/DLsqkWV6Cag?si=E5io0BqMhJ7EVlZE
Freya's Holmer legendary The Continuity of Splines video https://youtu.be/jvPPXbo87ds?si=nMoSacYif-rgTICE

Siedmiu, 2025-03-13:
Path smoothing test using SciPy implementations:
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

Siedmiu, 2025-03-15:
B-Spline is not adequate for our paths. I added a weight function that considers energy efficiency, accuracy and smoothness. The current graph shows paths focused on specific tasks, it is harder to optimise for smoothness and energy efficiency. Currently Natural Cubic Spline is the winner.

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

Siedmiu, 2025-03-15:
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

Closed 2025-05-31.

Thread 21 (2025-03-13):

Test print and assembly of Hexapod Leg

Siedmiu, 2025-03-13:
Produce and assemble the Hexapod Leg based on the CAD file. Test out all of the tolerances, range of motion, weight of the parts. Suggest improvements based on required strength, mass reduction and ease of assembly. Create step by step build guide.

Siedmiu, 2025-03-16:
General tolerance can be tightened, I will print version with updated servo dimensions tomorrow.

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

Closed 2025-05-31.

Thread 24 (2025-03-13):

Implementing hexapod model into gazebo

Bebo457, 2025-03-13:
- Correct models (STL files) so that they could be used in simulation (correcting pivot points f.e. in blender).
- Write appropriate SDF file to launch a simulation with correctly placed links, joints and physics of the elements and world.

Closed 2025-05-31.

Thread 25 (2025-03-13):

Controlling model in gazebo via ROS

Bebo457, 2025-03-13:
- Find a way to move certain links of a robot in simulation via ROS or other commands.
- Start implementing moving algorythm to move single leg

Siedmiu, 2025-05-31:
This issue was completed in March - I am closing it and moving to an archive.

Closed 2025-05-31.

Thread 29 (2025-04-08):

Implementing collision models into xacro files (gazebo)

Bebo457, 2025-04-08:
Problem:
In our current simulation model, the meshes responsible for detecting collisions of the robot are the same meshes used to visualize our model (STL files). This causes the simulator to perform more complex calculations to detect potential collisions, which drastically reduces the efficiency of the entire simulation.

Task:
We have already prepared, simplified models that should be implemented into the robot's Xacro code.

For questions regarding the simplified models, contact Grzechu.

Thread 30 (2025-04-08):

Implementing code to move all legs in simulation

Bebo457, 2025-04-08:
Problem:
Currently, we have code that can move a single leg.

Task:
Using this code as a base, create a new Python program that implements a basic walking algorithm, involving all six legs (or just more than one).

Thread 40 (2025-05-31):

[Task Recorded Late] New Hexapod Construction

Siedmiu, 2025-05-31:
### What was done?

After problems with the servos we have decided to switch to MG99R servos, which required a complete redesign of the Hexapod.
I have created new models for the Hexapod from the ground up. Models built up on the known strengths of the old design and addressed its main issues. Bigger servos also allowed for improved mechanical solutions and expanded range of motion.
I have also created separate models tailored for simulation as well as 3D printing models and instructions.
The new design will be describe in the mechanical documentation.

### Related Commits

Most of the design process, including new versions and version control is saved in the Fusion360 autodesk cloud storage. Which resulted in lack of commits on github.

Printing models and instruction commits:
0925162:
c1e5044:
72068f8:
f166ac5:

Simulation models:
4b07a6f:

### When was it done?

Majority of the work: May 18 - May 19, finishing the design and tweaking it May 20 - May 30

### Additional Notes

The majority of the construction including gear assemblies and leg assembly was done during May 18 - May 19.
May 20 -> the Hexapod platform base feature was finished and the initial models were avaluable for simulation.
After that the design was continuously modified and tested May 20 - May 30

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

Closed 2025-05-31.

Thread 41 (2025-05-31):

[Task Recorded Late] New Leg Assembly Testing

Siedmiu, 2025-05-31:
### What was done?

Before "full scale production" the hexapod leg assembly was printed, assembled and tested to validate it. Numerous parts have been adjusted or changed to ensure proper function and ease of assembly.

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

### Related Commits

_No response_

### When was it done?

May 19-25

### Additional Notes

_No response_

Closed 2025-05-31.

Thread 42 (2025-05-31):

Anti slip rubber tip research, design and testing

Siedmiu, 2025-05-31:
The Hexapod may encounter traction issues on smooth and slippery surfaces. Different shapes of rubber tip leg attachments will be designed and tested in order to adapt legs to different terrain.

Siedmiu, 2025-05-31:
I have created flat tip, flower, and latice structure design and I will compare them to the basic spherical design.

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

Siedmiu, 2025-06-04:
This issue will be marked as done when I commit all the files, documentation and research process notes.

Siedmiu, 2025-06-07:
I created new molds and casts,
the new leg design is 215% the volume of the previous, I also rounded out the edges to prevent cracking
Photo shows how the old design (mounted on the leg) compares to the new one
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

Siedmiu, 2025-06-11:
aa6f5e9 uploaded the documentation

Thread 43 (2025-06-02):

Contact sensor gazebo

Bebo457, 2025-06-02:
Implementing a Simulated Contact Sensor
(Gazebo Harmonic does not support it natively)

The goal is to determine whether the end effector (i.e., the tip of each leg) is in contact with the ground by estimating its global Z position. This involves reading the global position of the last link in each leg (the end_effector_link).

Update – 01.06.2025
Reading the position of a link relative to the robot's base frame is relatively straightforward, but this does not provide its global position.
There is a possibility that the odometry plugin could be used to achieve this functionality.

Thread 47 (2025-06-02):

move body with constant legs positions

FlyBozon, 2025-06-02:
- [x] implement some logic to move body relating to foots positions (currently we have logic that u can move legs relating to the platform, so it must be changed for our current goal or find some hack for that)
- [x] implement visualization in python - _optional_
- [x] implementation in Gazebo

Siedmiu, 2025-06-02:
What exactly are we planing to do here, and why is it required?

I don't think that it is possible to move the platform horizontally with big enough volume of movement without changing the position of the feet.
Positioning the platform UP and DOWN shouldn't be difficult to calculate since it only requires moving the joins in such a way that keeps their attachment point on one vertical axis. This shouldn't be difficult to calculate, or might even already be solved with the inverse kinematics equations.
Stick-bug side to side movements shouldn't be an issue either, but I don't see a reason for them.
Back and forth movements are interesting... I don't think we would be able to make long movements and avoid singularity points, but short ones may be possible. This could either be applied to readjust the position (especially with combination of 2 previous points) or intertwined with gait cycles to make the robot move faster - but very difficult.

There is another approach if our goal is to reach certain platform positions. We can try to estimate the best leg positions for a given platform position, but this is also difficult. I have already tried to implement that as a solution for curved path walking, where the platform was kept tangent to a given path. There is limited research online on how to do it, and my attempts were unsuccessful

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

FlyBozon, 2025-06-02:
@Siedmiu answering your question, that issue would be needed for uphill walking, to adjust platform position to compensate gravity impact. Idk if anyone else need that, but we can use it later to make robot dance, as once was told at the lecture - every robot should be able to dance (maybe it was told rather like - for some reason every robot can dance, but cannot do what they were created to, but nevertheless :D)

FlyBozon, 2025-06-24:
https://github.com/user-attachments/assets/f9501619-1c2f-43d9-ae1b-42393d639659

Closed 2025-06-24.

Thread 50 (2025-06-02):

[Task Recorded Late] Imu based trajectory

nickolaus125, 2025-06-02:
### What was done?

Created scripts allowing to get the data from IMU and proccess them in order to get the actual position of hexapod.
There are solutions using lower pass filtering like alpha filtering or butterorth filter to merge data from 2 imus to get rid of issues associated with the drift

### Related Commits

- c5f2788: files allowing to get date form IMU with Arduino board
- f67d423:  first algoritm with gravity filtering thanks to rotation matrixes
- 5d7de0a: report of issues and possible solutions
- 76e6f03: using on the board DMP to get already filtered data + simple comlementary filter to merge data from 2 imus
- b1ae833: Merging 2 IMUs data and butterworth filtering
- 9d24c80: test how getting and processing data work in real time instead of working on already written csv files - here with alpha filtering

### When was it done?

Late march - june

### Additional Notes

There is still some work to do to get appropriate postion in real time

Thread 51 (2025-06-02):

[Task Recorded Late] Inserting model of one leg into gazebo

Bebo457, 2025-06-02:
### What was done?

Task is to insert model of one robot leg based on STL files, into gazebo simulator.
- Determining the exact position and orientation of each leg and joint.
- Determining appropriate joint angle limits.

### Related Commits

- da0e064be282e1d79c5f4d1f1cf2dd5c3de670c1: Opening a robot leg model from AutoCad in gazebo
- ee6172766c930be09a8aea896a72229e749cdb5b: Adding .stl files of the splitted model
- d48f2c33a8cb89e4f4f308c8c1baaf3042ee9e3a: Implementing of all links of one leg and several joints
- c251ab77e2ce0f7422c6bd977ad988abb2205966: Adding corrected leg model stl files
- d026abbef6497aa308045b09144f6ec04a471f82: Adding joints
- 774e4d312a3f2f36b849c0c04894d625e4d13da7: Adding limits of joints rotation angles
- 3866bd4094ecf2c37adb82d22b9b42f62aec57f0: Adding the model's .urdf file
- 0e0a5c2bc2fe9bd29567c0fbfc4e9eeb60a44ff6: Updating links
- 8af93699c00dbf9973d02bbf809971a59dbe7fc8: Proper links and joins of one leg

### When was it done?

05.03.2025 - 26.03.2025

### Additional Notes

_No response_

Closed 2025-06-03.

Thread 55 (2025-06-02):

[Task Recorded Late] Configuring MoveIt to motion planning

Bebo457, 2025-06-02:
### What was done?

The task is to configure the MoveIt package and the simulation model to enable planning and executing the movement of each leg using RViz. The specific objectives are:
- Adding special links to the simulated robot model to serve as end effectors.
- Configuring MoveIt interactive markers, based on the OpenManipulator project.

### Related Commits

- f05e45170f43e526ea6c90bba3a6231a5a9c2864: I added moveit configuration package and new xaxcro versions with end effector links and joints. I corrected platform position and added hitbox for platform too.
- 65522b30276bb5a8d679b45d27ec66de8ab4564d: Improved motion planning in moveit, improved gazebo.launch.py

### When was it done?

26.04.2025 - 01.05.2025

### Additional Notes

None

Closed 2025-06-03.

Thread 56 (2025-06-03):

[Task Recorded Late] Opening the same robot model and controllers for both MoveIt (Rviz) and gazebo.

Bebo457, 2025-06-03:
### What was done?

The goal is to configure the entire system to use a unified robot model and controller setup, allowing motion simulation to be executed both via motion planning in RViz and through custom movement algorithms. The specific tasks include:
- Configuring the robot model to start with fixed initial joint positions.
- Ensuring the same robot model is used consistently throughout the system.
- Using a unified set of ROS controllers across the entire system.

### Related Commits

- 740184549e7003434556d3acebe8b465f01db397: research for starting position in gazebo
- f4ec29bd96a4cfb663794824e2a2501de2cd6d49: trying to set starting positions in gazebo
- 9d9920a20bb4297d5118dfef0d4048cca6c54e73: I fixed the incorrect display of the model in gazebo. I removed unnecessary stl files. I added loading by gazebo of ROS2 controllers.
- e87a558b94a3497bec95e0fc7f1d67b7063cc698: Loading the same model for Gazebo and MoveIt

### When was it done?

26.04.2025 - 09.05.2025

### Additional Notes

None

Closed 2025-06-03.

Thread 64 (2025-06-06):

Servo ROM pulse width

Siedmiu, 2025-06-06:
Our current settings for SERVO_MIN and SERVO_MAX values do not cover the whole range of motion, this will interfere with our walk cycles, zero positions AND GEAR ALIGNMENT.
This needs to be fixed ASAP!

Siedmiu, 2025-06-06:
I spent a few hours testing the correct limits and for 60Hz frequency the correct limits are:
const int SERVO_MIN = 90;
const int SERVO_MAX = 600;
const int PWM_FREQUENCY = 60;
But everywhere on the internet I see that the 50Hz is the correct frequency for our servos, and apparently running them at 60Hz for prolonged amount of time can cause damage to them.
I will now re do the testing to find out the correct limits for 50Hz.
Also switching the limits means that we have to readjust every gearbox on the Hexapod

Siedmiu, 2025-06-07:
I used a more accurate testing method. Right now the correct settings are:
const int SERVO_MIN = 104;
const int SERVO_MAX = 490;
const int PWM_FREQUENCY = 50; //Hz

alternatively for 60Hz:
const int SERVO_MIN = 125;
const int SERVO_MAX = 588;
const int PWM_FREQUENCY = 60;
but we won't use this, as the 60Hz is most likely incorrect for our servos

Siedmiu, 2025-06-07:
Main repo: fe62f38 change in zeroing code
Sim repo: 991b2b7

Closed 2025-06-07.

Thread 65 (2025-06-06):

Robust pinion-servo attatchment

Siedmiu, 2025-06-06:
The current servo attachment method needs reinforcement, the pinions have to be fixed.

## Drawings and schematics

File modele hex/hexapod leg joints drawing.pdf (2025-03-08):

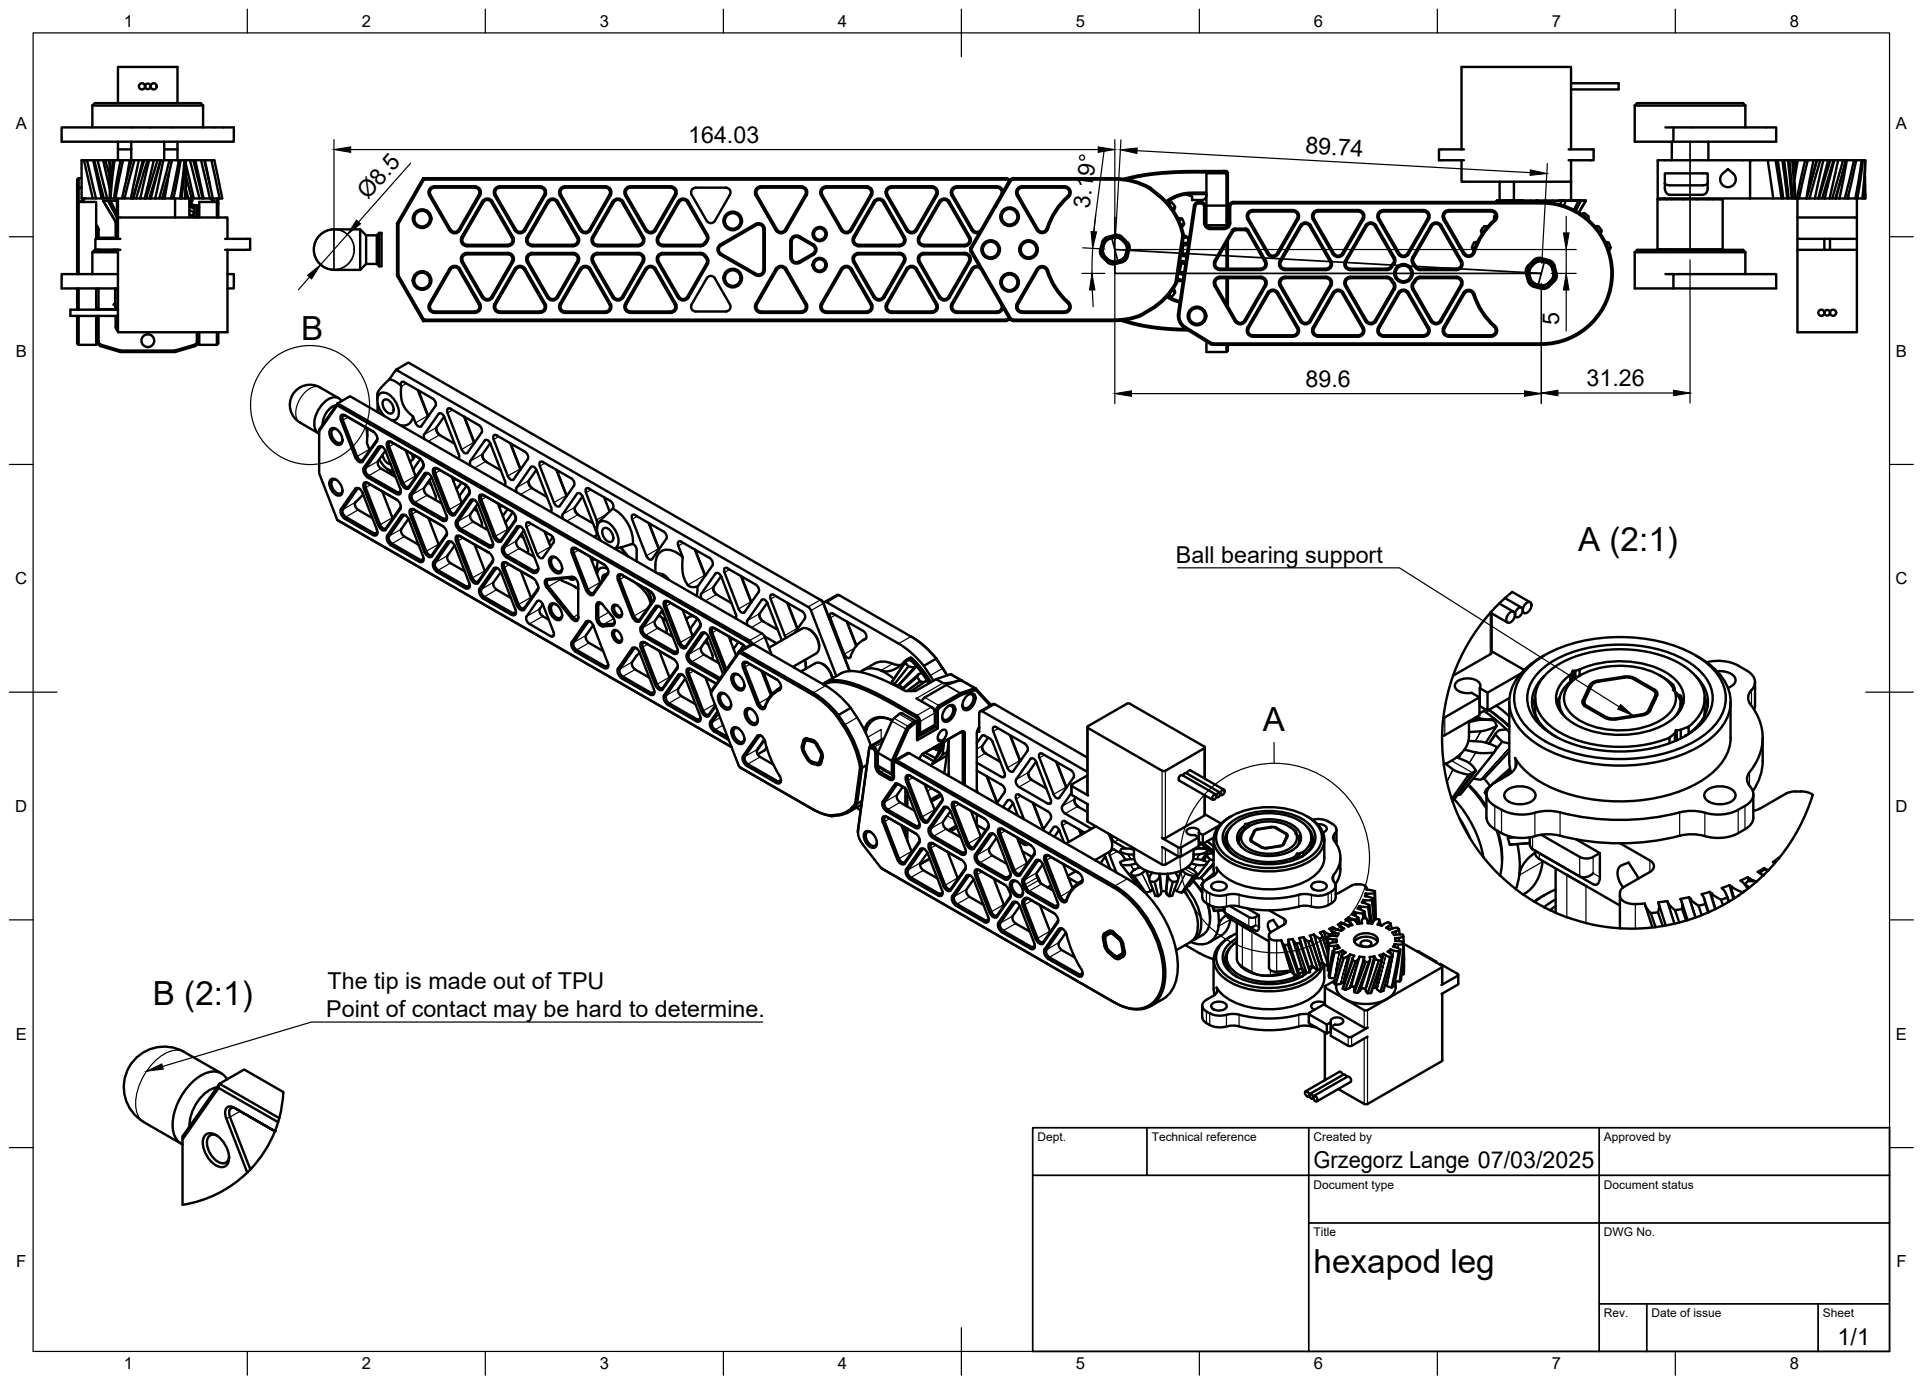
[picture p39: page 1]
Dept.; Technical reference; Created by; Approved by; Document type; Document status; Title; DWG No.; Rev.; Date of issue; Sheet; hexapod leg; Grzegorz Lange

Ball bearing support

The tip is made out of TPU
Point of contact may be hard to determine.

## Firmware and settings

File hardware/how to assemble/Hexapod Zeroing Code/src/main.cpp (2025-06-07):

#include <Wire.h>
#include <Adafruit_PWMServoDriver.h>

// Mapowanie serw
// joint1_3 -> 0, ..., joint3_4 -> 17

// WiFi NIE jest potrzebne
// const char* ssid = "EspHex";
// const char* password = "74835915";

// Sterowniki PCA9685


// # Mapowanie nazw jointów na numery serw
// joint_to_servo = {
//     "joint1_3": 0,
//     "joint2_3": 1,
//     "joint3_3": 2,
//     "joint1_2": 3,
//     "joint2_2": 4,
//     "joint3_2": 5,
//     "joint1_1": 6,
//     "joint2_1": 7,
//     "joint3_1": 8,
//     "joint1_6": 9,
//     "joint2_6": 10,
//     "joint3_6": 11,
//     "joint1_5": 12,
//     "joint2_5": 13,
//     "joint3_5": 14,
//     "joint1_4": 15,
//     "joint2_4": 16,
//     "joint3_4": 17,
// }

Adafruit_PWMServoDriver pwm1 = Adafruit_PWMServoDriver(0x40);
Adafruit_PWMServoDriver pwm2 = Adafruit_PWMServoDriver(0x41);

//DO NOT CHANGE, THOSE VALUES DETERMINE THE STARTING AND ENDING POSITIONS OF THE SERVO
const int SERVO_MIN = 104;
const int SERVO_MAX = 490;
const int PWM_FREQUENCY = 50;

void setServoAngle(uint8_t servoIndex, float angle) {
  angle = constrain(angle, 0, 180);
  uint16_t pulse = map(angle, 0, 180, SERVO_MIN, SERVO_MAX);

  if (servoIndex >= 0 && servoIndex < 9) {
    pwm1.setPWM(servoIndex, 0, pulse);
  } else if (servoIndex >= 9 && servoIndex < 18) {
    pwm2.setPWM(servoIndex - 9, 0, pulse);
  } else {
    Serial.println("Invalid servo index.");
  }
}

void parseAndHandleCommand(String msg) {
  msg.trim();
  //Serial.printf("Received: '%s'\r\n", msg.c_str());

  if (msg.startsWith("servo")) {
    int servoNum = -1;
    int angle = -1;

    int digitPos = 5;
    while (digitPos < msg.length() && !isDigit(msg[digitPos])) {
      digitPos++;
    }

    int spacePos = msg.indexOf(' ', digitPos);
    if (spacePos != -1) {
      String servoStr = msg.substring(digitPos, spacePos);
      String angleStr = msg.substring(spacePos + 1);

      servoNum = servoStr.toInt();
      angle = angleStr.toInt();

      if(servoNum==13){
        
        Serial.printf("Parsed: servo=%d, angle=%d\r\n", servoNum, angle);
      }

      if (servoNum >= 0 && servoNum <= 17 && angle >= 0 && angle <= 180) {
        // if (servoNum == 9 || servoNum == 12 || servoNum == 15 || servoNum % 3 == 2) { // || servoNum % 3 == 1
        //   angle = 180 - angle;
        // }
        setServoAngle(servoNum, angle);
        if (servoNum == 13) {
          Serial.printf("Servo %d moved to %d°\r\n", servoNum, angle);
        }
        
      } else {
        Serial.printf("Invalid servo number (%d) or angle (%d). Allowed: 0-17, 0-180\r\n",servoNum, angle);
      }
    } else {
      Serial.println("Invalid command format. Expected: 'servo<number> <angle>'");
    }
  } else {
    Serial.printf("Unknown command: '%s'\r\n", msg.c_str());
  }
}

void setup() {
  Serial.begin(115200);
  Wire.begin();

  pwm1.begin();
  pwm1.setPWMFreq(PWM_FREQUENCY);
  pwm2.begin();
  pwm2.setPWMFreq(PWM_FREQUENCY);
  Serial.println("Both PCA9685 initialized.");

  int all_j1_angle = 0;
  int all_j2_angle = 135;
  int all_j3_angle = 180;
  // joint 1
  setServoAngle(0, all_j1_angle);
  setServoAngle(3, all_j1_angle);
  setServoAngle(6, all_j1_angle);
  setServoAngle(9, all_j1_angle);
  setServoAngle(12, all_j1_angle);
  setServoAngle(15, all_j1_angle);

  // joint 2
  setServoAngle(1, all_j2_angle);
  setServoAngle(4, all_j2_angle);
  setServoAngle(7, all_j2_angle);
  setServoAngle(10, all_j2_angle);
  setServoAngle(13, all_j2_angle);
  setServoAngle(16, all_j2_angle);
  // joint 3
  setServoAngle(2, all_j3_angle);
  setServoAngle(5, all_j3_angle);
  setServoAngle(8, all_j3_angle);
  setServoAngle(11, all_j3_angle);
  setServoAngle(14, all_j3_angle);
  setServoAngle(17, all_j3_angle);
}
  

void loop() {
  static String inputString = "";
  while (Serial.available()) {
    char c = (char)Serial.read();
    if (c == '\n' || c == '\r') {
      if (inputString.length() > 0) {
        parseAndHandleCommand(inputString);
        inputString = "";
      }
    } else {
      inputString += c;
    }
  }
  int all_j1_angle = 180;   //90
  int all_j2_angle = 90;    //90
  int all_j3_angle = 0;    //135
  // joint 1
  setServoAngle(0, all_j1_angle);
  setServoAngle(3, all_j1_angle);
  setServoAngle(6, all_j1_angle);
  setServoAngle(9, all_j1_angle);
  setServoAngle(12, all_j1_angle);
  setServoAngle(15, all_j1_angle);

  // joint 2
  setServoAngle(1, all_j2_angle);
  setServoAngle(4, all_j2_angle);
  setServoAngle(7, all_j2_angle);
  setServoAngle(10, all_j2_angle);
  setServoAngle(13, all_j2_angle);
  setServoAngle(16, all_j2_angle);
  // joint 3
  setServoAngle(2, all_j3_angle);
  setServoAngle(5, all_j3_angle);
  setServoAngle(8, all_j3_angle);
  setServoAngle(11, all_j3_angle);
  setServoAngle(14, all_j3_angle);
  setServoAngle(17, all_j3_angle);
}

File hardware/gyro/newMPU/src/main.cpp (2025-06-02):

//uses Jeff Rowberg's I2Cdev and MPU6050 libraries which are open source and MIT licence
//https://www.i2cdevlib.com/

#include <Wire.h>
#include "I2Cdev.h"
#include "MPU6050_6Axis_MotionApps20.h"

void calibrateMPU6050(); //not used currently
void sendDataToSerial();

//MPU control
MPU6050 mpu;
bool dmpReady = false;  //true if DMP init was successful
uint8_t mpuIntStatus;   //holds interrupt status
uint8_t devStatus;      //status after each device operation
uint16_t packetSize;    //DMP packet size (default is 42 bytes)
uint16_t fifoCount;     // count of all bytes currently in FIFO
uint8_t fifoBuffer[64]; // FIFO storage buffer

// orientation, motion
Quaternion q;           // [w, x, y, z]
VectorInt16 aa;         // [x, y, z]            accel sensor measurements
VectorInt16 aaReal;     // [x, y, z]            gravity-free compensated accel
VectorInt16 aaWorld;    // [x, y, z]            world-frame accel sensor measurements
VectorFloat gravity;    // [x, y, z]
float ypr[3];           // [yaw, pitch, roll]

//sensor settle time
unsigned long startTime = 0;
bool initialPeriodComplete = false;
const unsigned long INITIAL_PERIOD_MS = 17000;

//MPU interrupt detection
volatile bool mpuInterrupt = false;
void IRAM_ATTR dmpDataReady() {
    mpuInterrupt = true;
}

void setup() {
    Serial.begin(115200);
    while (!Serial);

    //I2C
    Wire.begin(26, 25); // SDA, SCL pins, define as constants
    Wire.setClock(400000); //400kHz

    Serial.println("Initializing MPU6050...");
    mpu.initialize();
    Serial.println("Testing device connections...");
    Serial.println(mpu.testConnection() ? "MPU6050 connection successful" : "MPU6050 connection failed");
    Serial.println("Initializing DMP...");
    devStatus = mpu.dmpInitialize();
    
    //initialize ofsets before callibration
    mpu.setXGyroOffset(0);
    mpu.setYGyroOffset(0);
    mpu.setZGyroOffset(0);
    mpu.setXAccelOffset(0);
    mpu.setYAccelOffset(0);
    mpu.setZAccelOffset(0);
    
    //DMP initialization check
    if (devStatus == 0) {
        //Serial.println("Calibrating MPU6050...");
        //calibrateMPU6050();
        Serial.println("Enabling DMP...");
        mpu.setDMPEnabled(true);
        
        //enable interrupt detection
        Serial.println("Enabling interrupt detection (ESP32 pin 27)...");
        attachInterrupt(27, dmpDataReady, RISING);
        mpuIntStatus = mpu.getIntStatus();
        
        Serial.println("DMP ready! Waiting for first interrupt...");
        dmpReady = true;
        
        // get packet size
        packetSize = mpu.dmpGetFIFOPacketSize();

        //settle time
        startTime = millis();
        Serial.println("Waiting for the sensor to settle...");
    } else {
        // ERROR!
        // 1 = initial memory load failed
        // 2 = DMP configuration updates failed
        Serial.print("DMP Initialization failed (code ");
        Serial.print(devStatus);
        Serial.println(")");
    }
}

void loop() {
    if (!dmpReady) return;
    if (!mpuInterrupt && fifoCount < packetSize) return;
    
    mpuInterrupt = false;
    mpuIntStatus = mpu.getIntStatus();

    if (!initialPeriodComplete && (millis() - startTime > INITIAL_PERIOD_MS)) {
        initialPeriodComplete = true;
        Serial.println("INIT_COMPLETE");
    }

    // Check for overflow
    fifoCount = mpu.getFIFOCount();
    if ((mpuIntStatus & 0x10) || fifoCount == 1024) {
        mpu.resetFIFO();
        Serial.println("FIFO overflow!");
    
    } else if (mpuIntStatus & 0x02) {
        while (fifoCount < packetSize) fifoCount = mpu.getFIFOCount();
        
        // Read a packet from FIFO
        mpu.getFIFOBytes(fifoBuffer, packetSize);
        fifoCount -= packetSize;
        
        mpu.dmpGetQuaternion(&q, fifoBuffer);
        mpu.dmpGetGravity(&gravity, &q);
        mpu.dmpGetYawPitchRoll(ypr, &q, &gravity);
        mpu.dmpGetAccel(&aa, fifoBuffer);
        mpu.dmpGetLinearAccel(&aaReal, &aa, &gravity);
        mpu.dmpGetLinearAccelInWorld(&aaWorld, &aaReal, &q);
        
        if (initialPeriodComplete) {
            sendDataToSerial();
        }
    }
}

void calibrateMPU6050() {
    const int numSamples = 2000;  // Number of samples for calibration
    const int settleTime = 2000;  // setteling delay
    
    //calibration sums
    int32_t ax_sum = 0, ay_sum = 0, az_sum = 0;
    int32_t gx_sum = 0, gy_sum = 0, gz_sum = 0;
    
    //Serial.println("Letting sensor settle...");
    //delay(settleTime);
    Serial.println("Collecting calibration samples...");
    for (int i = 0; i < numSamples; i++) {
        int16_t ax, ay, az, gx, gy, gz;
        mpu.getMotion6(&ax, &ay, &az, &gx, &gy, &gz);
        
        ax_sum += ax;
        ay_sum += ay;
        az_sum += az;
        gx_sum += gx;
        gy_sum += gy;
        gz_sum += gz;
        
        delay(2);
    }
    
    int16_t ax_mean = ax_sum / numSamples;
    int16_t ay_mean = ay_sum / numSamples;
    int16_t az_mean = az_sum / numSamples;
    int16_t gx_mean = gx_sum / numSamples;
    int16_t gy_mean = gy_sum / numSamples;
    int16_t gz_mean = gz_sum / numSamples;
    
    //compensate for gravity in z-axis (~16384 at rest with 2g sensitivity setting)
    //??? this won't work, what if the sensor is at an angle?
    //az_mean -= 16384;  
    
    //Set offsets
    mpu.setXAccelOffset(-ax_mean);
    mpu.setYAccelOffset(-ay_mean);
    mpu.setZAccelOffset(-az_mean);
    mpu.setXGyroOffset(-gx_mean);
    mpu.setYGyroOffset(-gy_mean);
    mpu.setZGyroOffset(-gz_mean);
    
    Serial.println("Calibration complete!");
    delay(100);
}

void sendDataToSerial() {
    // Timestamp
    Serial.print(millis());
    Serial.print(",");
    
    // Quaternion
    Serial.print(q.w);
    Serial.print(",");
    Serial.print(q.x);
    Serial.print(",");
    Serial.print(q.y);
    Serial.print(",");
    Serial.print(q.z);
    Serial.print(",");
    
    // Euler angles (in degrees)
    Serial.print(ypr[0] * 180/M_PI); // Yaw
    Serial.print(",");
    Serial.print(ypr[1] * 180/M_PI); // Pitch
    Serial.print(",");
    Serial.print(ypr[2] * 180/M_PI); // Roll
    Serial.print(",");
    
    // Raw acceleration
    //this value doesn't change, why?
    Serial.print(aa.x);
    Serial.print(",");
    Serial.print(aa.y);
    Serial.print(",");
    Serial.print(aa.z);
    Serial.print(",");
    
    // World acceleration (gravity compensated)
    Serial.print(aaWorld.x);
    Serial.print(",");
    Serial.print(aaWorld.y);
    Serial.print(",");
    Serial.print(aaWorld.z);
    
    Serial.println();
}

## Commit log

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2025-02-22 Hexapod leg assembly step file.
    See issue comments for description.
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2025-03-01 Delete modele hex/hexapod leg v15.step
    Has been replaced by new version hexapod leg v20
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2025-03-02 STL files for 3D printed ball bearings
    Discussed in sub issue
    [ball bearing 1_4_''.stl, ball bearing 3_16_''.stl]
2025-03-05 Otworzenie modelu nogi robota z AutoCada w gazebo
    W celu przekonwertowania modelu z AutoCada do pliku STL (lub innego obsługiwanego) można użyć programu freeCAD. Dostępny jest w app center Ubuntu. Filmik na yt, dokładnie pokazujący jak eskportować
    https://www.youtube.com/watch?v=d_vdUgTZqag&ab_channel=CADCAMLessons
    W pliku zip znajduje się plik dae, na wypadek jakby stl nam nie wsytarczał (lepszy ale zdecydowanie cięższy format)
    [leg_model.sdf]
2025-03-08 Dostosowanie kodu do modelu składającego się z kilku plików .stl oraz rozwinięcie cech elementów.
    [leg_model.sdf]
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2025-03-11 Wprowadzenie wszystkich linków jednej nogi i kilku jointów
    Dodano linki kolejne linki nogi, wraz z komentarzami oraz jointy między platformą a przekładnią platformy, platformą a górną częścią nogi, górną częścią nogi a górną przekładnią oraz górną przekładni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
    [leg_model.sdf]
2025-03-11 Dodawanie poprawionych plików stl modelu nogi
    W poprawionych plikach, środki mas (pivot pointy) zostały przeniesione do geometrycznego środka poszczególnych części.
    [leg_down.stl, leg_mid.stl, leg_mid_gear.stl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]
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2025-03-12 Dodanie jointów
    Do nogi zostały dodane poprawnie umieszczone joiny. Nie zostały jeszcze zdefiniowane odpowiednie ograniczenia na ruch kątów. Na razie są ustawione na +/- nieskończoność.
    [leg_model.sdf]
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2025-03-16 Dodanie ograniczeń na kąty obrotów linków
    Ograniczenia zgodne z tymi, które przedstawiliśmy na prezentacji.
    [leg_model.sdf]
2025-03-21 Dodanie struktury plików ROS i działający bridge, (gz_ros2_control nie działa)
    [hexapod.sdf, leg_down.stl, leg_mid.stl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]
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2025-03-22 Początek integracji modelu z ROSem
    W pliku README.md umieściłem dokładniejszy opis/instrukcję tego co się tutaj dzieje
    [hexapod.xacro, leg_down.stl, leg_mid.stl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]
2025-03-22 added simplified xacro file with all 6 legs
    simplified xacro file with all 6 legs, for moveit simulation. TODO: correct joints points and check the angles that each part of the leg can reach (hadn't found documentation on that in our folders, so added simple 30* symmetrically and for the upper leg 15* up and 45 down, which must be +- what we wanted or what was told one day, but must be checked and corrected if needed)
    [hexapod.xacro]
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2025-03-23 solved problems from underprevious commit
    modified angles for each leg, their length and origin points
    TODO: get inertia from previous commit and add it to that xacro file. At that moment when trying to connect those files, they dont work together (on my computer xacro with modified inertia also doesnt work, so the problem may be on inertia side)
    [hexapod.xacro]
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2025-03-23 creates a moveit configuration files
    creates a moveit configuration files based on tutorial from following video https://www.youtube.com/watch?v=5dAHoK9BbgE (for ros noetic, but not too much modifications were needed)
    to use that tool you need to run the following command, and then based on the tutorial (only general info in the video, but hexapod is much more complex, and if you have question, u can reach me out) and hexapod.xacro file.
    commands for that tool:
    sudo apt-get install ros-jazzy-moveit ros-jazzy-moveit-plugins ros-jazzy-moveit-planners
    ros2 launch moveit_setup_assistant setup_assistant.launch.py
    for now i cannot open the created files in rviz, the problem is with loadin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
    [hexapod.ros2_control.xacro, hexapod.urdf.xacro, hexapod.xacro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]
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2025-03-23 Dodalem pliki pozwalajace na odpalenie modelu w Rviz i gazebo
    [enclosure.sdf, hexapod.urdf, leg_down.stl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]
2025-03-24 Mozna odpalic ros2 launch hexapod_moveit_config demo.launch.py i ustawic jakis ruch w Rviz
    [hexapod.ros2_control.xacro, hexapod.urdf.xacro, joint_limits.yaml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]
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2025-03-26 Nominal gear fix
    [Nominal gear.stl, pinion 24.stl]
2025-03-27 combined files to run simulation in gz and rviz
    [hexapod.sdf, leg_down.stl, leg_mid.stl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]
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2025-04-01 Dodalem nowy worspace ros, stworzony na podstawie przykladu, ktory mozna odpalic z hexapodem
    [empty_world.sdf, gazebo_controller_manager.yaml, gravity_compensation_controller_parameters.yaml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]
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2025-04-03 added inertia
    TODO: update legs data after we move to new hexapod model, now length/radiu etc are from old model
    [open_manipulator_x_arm.urdf.xacro]
2025-04-03 dodalem do cmakelist nasz plik exe, usunalem poprzednie zmiany inercji, stworzylem wstepnie pliki do hexapoda nieprzymocowanego
    [empty_world.sdf, gazebo_controller_manager.yaml, hardware_controller_manager.yaml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]
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2025-04-07 wstawione prawidlowe modele nogi 5 i poprawione linki i jointy nogi 5
    [leg_down.stl, leg_mid.stl, leg_up.stl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]
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2025-04-08 I cleaned up the ros2_ws_hex file structure and added a little documentation in the README
    [1_leg_down.stl, 1_leg_mid.stl, 1_leg_up.stl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]
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2025-04-10 I added launch files for floating, static model in gazebo and rviz launch. Fixed limitations of angles of joints
    [1_leg_down.stl, 1_leg_mid.stl, 1_leg_up.stl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]
2025-04-12 source of issues and possible solutions research
    In this file I described what I found about current issues - they seems to be inevitable using our way of navigating. Unfortunately proposed solutions seem to not be easy to implemented in our project
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2025-04-19 Alternative MPU trajectory using DMP
    Our MPU module has an onboard digital motion processor chip that can be used to correct the drift.
    The system connects Matlab directly to the esp.
    This is the latest working version, but it is outdated since I started working on proper filters.
    [main.cpp]
2025-04-26 I added moveit configuration package and new xaxcro versions with end effector links and joints. I corrected platform position and added hitbox for platform too
    [hexapod.ros2_control.xacro, hexapod.urdf.xacro, hexapod_ee.urdf.xacro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]
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2025-04-26 Update hexapod_leg_ee.urdf.xacro
    Adding code that may be helpful in starting leg position
    [hexapod_leg_ee.urdf.xacro]
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2025-05-01 dodanie pozycji + ruch w motion planning poprzez plik pythonowy
    [hexapod_leg_ee.urdf.xacro]
2025-05-02 Joint 1 and 3 reinforcement
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2025-05-04 I added simpler collision models, that are accepted by gazebo simulator. Now we use only one model for each leg.
    [down_section_hitbox.xacro, hexapod.urdf.xacro, hexapod_leg.urdf.xacro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]
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2025-05-09 I fixed the incorrect display of the model in gazebo. I removed unnecessary stl files. I added loading by gazebo of ROS2 controllers.
    [1_leg_down.stl, 1_leg_mid.stl, 1_leg_up.stl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]
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2025-05-09 fixed misatke with minus
    in movit our second joint was a negative value of mine here
2025-05-09 fixed mistake with minus
    in movit second joint was a negative value of mine here
2025-05-09 Loading the same model for Gazebo and MoveIt
    [hexapod.ros2_control.xacro, hexapod.urdf.xacro, hexapod_ee.urdf.xacro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]
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2025-05-10 Corrected few physics properties
    [empty_ode.sdf, hexapod_leg_ee.urdf.xacro]
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2025-05-10 added an opportunity to run simulation and real robot code from one file, using parameter
    [down_section_hitbox.xacro, empty_ode.sdf, empty_world.sdf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]
2025-05-10 added an opportunity to run simulation and serwer for real robot using parameter, rearanged corresponding files on repo
    [down_section_hitbox.xacro, empty_ode.sdf, empty_world.sdf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]
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2025-05-13 added imu, started connections between app and real robot'
    [down_section_hitbox.xacro, empty_ode.sdf, empty_world.sdf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]
2025-05-14 adjusting xacro to inertia, adding inertia to xacro
    [hexapod_leg_ee.urdf.xacro]
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2025-05-23 moved everything connected to robot to sim_and_real folder
    [hexapod_leg_ee.urdf.xacro]
2025-05-23 added camera.xacro from camera_integration branch, updated sim README
    [camera.xacro]
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2025-05-23 I added new robot model to the simulation and optimized simulation for both models. New model on default. Old model gazebov1.launch.py
    [hexapod.urdf.xacro, hexapod_ee.urdf.xacro, hexapod_eeV1.urdf.xacro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]
2025-05-25 added collision model for new robot, collision of tip is now in end_effecor_link, collision in this link seems to mess something with rviz, but gazebo seems to work properly
    [down_section_hitbox.xacro, hexapod_leg_ee.urdf.xacro, mid_section_hitbox.xacro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]
2025-05-26 I deleted unnecesary packages and fixed collision error in moveit
    [gravity_compensation_controller_parameters.yaml, hexapod_leg_ee.urdf.xacro, spring_actuator_controller_parameters.yaml]
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2025-05-26 Started implementing proper hardware interface. Fake hardware is working
    [hexapod.ros2_control.xacro, hexapod.urdf.xacro, hexapod_ee.urdf.xacro]
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2025-05-28 Printing Sesion 2 and 3
    Printing files and instructions for the rest of the mid section and down section truss.
    [Bevel_gear_shaft.stl, Bevel_gear_shaft_cap.stl, Down Section Truss Back 1.stl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]
2025-05-29 alpha filtering data in real time
    Alpha filter could be useful to filter acceleration data before rotations and merging data from 2 IMU's together to eliminate drift
    [rt_alpha_filtering.py]
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2025-05-30 update import shell files to be compatible with current setup files, minor bugs fixed
2025-05-30 Fixed minor issue with moveit and created seperate moveit launch to work with hardware
    [hexapod_hardware.urdf.xacro]
2025-05-31 Reorganized repo: moved documentation, hardware, and gallery files
    [BL1.stl, BL2.stl, BL3.stl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]
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2025-06-04 Report on current isses and possible solutions
    This report describes wat was done in oreder to get more appropriate trajectory based on IMU data. It also has some possible explanations why methods already used fails in many fields
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2025-06-07 3D files for the latest design of the silicone mold
    3D files for the latest design of the silicone mold used to create the silicone/ rubber leg tips for the best anti slip efficiency
    [Mold Stif Out.stl, Mold Stiff In.stl]
2025-06-09 Another approach using federated filters
    This attempt has some issues overfiltering in the Y and Z axis
    [federated_filters.py]
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
